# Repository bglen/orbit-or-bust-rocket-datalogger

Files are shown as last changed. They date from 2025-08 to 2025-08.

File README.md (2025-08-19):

# Rocket Datalogger

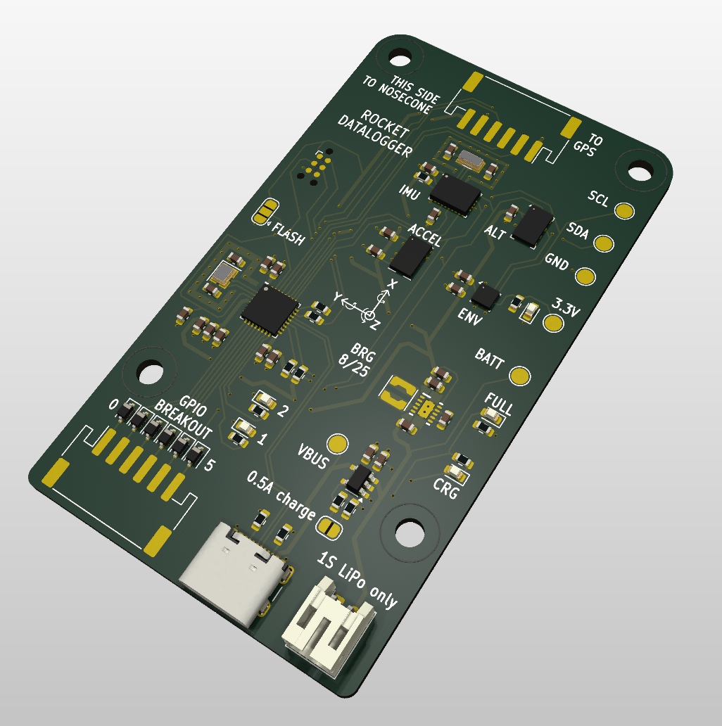
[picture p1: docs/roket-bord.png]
Roket bord


This is an STM32-based model rocket datalogger. It logs from the following sensors:

- DAN-F10-00B ublox dual band GNSS module
- ADXL375 high G accelerometer
- BNO055 9-DOF inertial measurement unit
- MS5607-02BA high resolution altimeter sensor
- BME280 humidity, pressure and temperature sensor

The board is powered from a single 1S LiPo battery with a standard JST-PH connector. A USB-C connector is provided for downloading the flight data. a 6-pin JST-PH connector is provided to extend the device's functionality with 6 3.3V-level GPIO pins.

The GNSS module is on a seperate PCB connected with a JST-PH connector, to give the integrated antenna the appropriate orientation (facing the sky).

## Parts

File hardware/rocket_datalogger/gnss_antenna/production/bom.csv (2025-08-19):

Designator | Footprint | Quantity | Value | LCSC Part #
J1 | JST_PH_S6B-PH-SM4-TB_1x06-1MP_P2.00mm_Horizontal | 1 | JST-PH-S6B-SM4_TB
U1 | DAN-F10-00B | 1 | ~

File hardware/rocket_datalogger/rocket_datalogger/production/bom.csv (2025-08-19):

Designator | Footprint | Quantity | Value | LCSC Part #
C1, C12, C17, C18, C19, C21, C22, C23, C4, C5, C6 | 0603 | 11 | 0.1uF
C10 | 0603 | 1 | 1uF
C11 | 0603 | 1 | 10 uF
C13, C14 | 0603 | 2 | 10uF
C15, C16 | 0603 | 2 | 10uF 6.3V
C2, C3 | 0603 | 2 | 4.7uF
C20 | 0603 | 1 | 1uF Tantalum
C24, C25 | 0603 | 2 | 22 pF
C7, C9 | 0603 | 2 | 12pF
C8 | 0603 | 1 | 10nF
D1, D2, D3, D4, D5, D6 | D_SOD-323 | 6 | PESD3V3L1BA
D10 | 0603 | 1 | Red LED
D11 | 0603 | 1 | Green LED
D7, D8, D9 | 0603 | 3 | LED
J2, J6 | JST_PH_S6B-PH-SM4-TB_1x06-1MP_P2.00mm_Horizontal | 2 | JST-PH-S6B-SM4_TB
J3 | Tag-Connect_TC2030-IDC-NL_2x03_P1.27mm_Vertical | 1 | TC2030
J4 | JST_PH_S2B-PH-K_1x02_P2.00mm_Horizontal | 1 | JST-PH 1x2
J5 | USB_C_Receptacle_GCT_USB4105-xx-A_16P_TopMnt_Horizontal | 1 | USB_C_Receptacle_USB2.0_16P
JP1 | SolderJumper-3_P1.3mm_Open_RoundedPad1.0x1.5mm | 1 | Jumper_3_Open
JP2 | SolderJumper-2_P1.3mm_Open_RoundedPad1.0x1.5mm | 1 | Jumper_2_Open
L1 | L_Coilcraft_LPS3010 | 1 | 1.5uH LPS3015-152MRC
R1, R2 | 0603 | 2 | 5.1k
R10 | 0603 | 1 | 2.2k
R11, R14 | 0603 | 2 | 10k
R12, R13 | 0603 | 2 | 470
R3, R4, R9 | 0603 | 3 | 1k
R5, R6 | 0603 | 2 | 22
R7, R8 | 0603 | 2 | 4.7k
TP1 | TestPoint_Pad_D2.0mm | 1 | TestPoint
TP2 | TestPoint_Pad_D2.0mm | 1 | BATT
TP3 | TestPoint_Pad_D2.0mm | 1 | 3V3
TP4 | TestPoint_Pad_D2.0mm | 1 | GND
TP5 | TestPoint_Pad_D2.0mm | 1 | SCL
TP6 | TestPoint_Pad_D2.0mm | 1 | SDA
U1 | QFN-32-1EP_5x5mm_P0.5mm_EP3.45x3.45mm | 1 | STM32F042K6Ux
U2 | DSK0010A | 1 | ~
U3 | SOT-23-5 | 1 | MCP73831-2-OT
U4 | LGA-8_3x5mm_P1.25mm | 1 | MS5607-02BA
U5 | Bosch_LGA-8_2.5x2.5mm_P0.65mm_ClockwisePinNumbering | 1 | BME280
U7 | LGA-14_3x5mm_P0.8mm_LayoutBorder1x6y | 1 | ~
U8 | LGA-28_5.2x3.8mm_P0.5mm | 1 | BNO055
Y1 | Crystal_SMD_2520-4Pin_2.5x2.0mm | 1 | ECS-160-10-36Q-AES-TR
Y2 | Crystal_SMD_3215-2Pin_3.2x1.5mm | 1 | ECX-.327-CDX-1293

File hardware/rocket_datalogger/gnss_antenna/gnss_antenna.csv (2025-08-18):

Reference | Value | Footprint | Datasheet | Qty | DNP | Exclude from BOM | Exclude from Board
C1,C2 | 4.7uF | Capacitor_SMD:C_0603_1608Metric | ~ | 2
C3,C4,C5,C6,C12,C14,C15 | 0.1uF | Capacitor_SMD:C_0603_1608Metric | ~ | 7
C7,C9 | 12pF | Capacitor_SMD:C_0603_1608Metric | ~ | 2
C8 | 10nF | Capacitor_SMD:C_0603_1608Metric | ~ | 1
C10,C11 | 1uF | Capacitor_SMD:C_0603_1608Metric | ~ | 2
C13 | 22uF | Capacitor_SMD:C_0805_2012Metric | ~ | 1
C16,C17 | 10uF | Capacitor_SMD:C_0603_1608Metric | ~ | 2
D1,D2,D3,D22 | LED | LED_SMD:LED_0603_1608Metric | ~ | 4
D4 | NUP2105L | Package_TO_SOT_SMD:SOT-23 | http://www.onsemi.com/pub_link/Collateral/NUP2105L-D.PDF | 1
D5,D6,D7,D8,D13,D14,D15,D16 | PESD3V3L1BA | Diode_SMD:D_SOD-323 | ~ | 8
D9,D10,D11,D12,D17,D18,D19,D20 | BAT54S | Package_TO_SOT_SMD:SOT-23 | https://www.diodes.com/assets/Datasheets/ds11005.pdf | 8
D21 | CDBW140-G | Diode_SMD:D_SOD-123 | http://www.diodes.com/_files/datasheets/ds23022.pdf | 1
H1,H2,H3,H4 | MountingHole | MountingHole:MountingHole_3.2mm_M3 | ~ | 4 |  | Excluded from BOM
J1 | AMP_Superseal_9-6437287-8 | signal_to_can:TE_9-6437287-8_1 |  | 1
J2 | TC2030 | Connector:Tag-Connect_TC2030-IDC-NL_2x03_P1.27mm_Vertical | ~ | 1
JP1 | Jumper_3_Open | Jumper:SolderJumper-3_P1.3mm_Open_RoundedPad1.0x1.5mm | ~ | 1
R1,R2 | 22 | Resistor_SMD:R_0603_1608Metric | ~ | 2
R3,R4,R5,R14 | 1k | Resistor_SMD:R_0603_1608Metric | ~ | 4
R6,R7,R8,R9,R10,R11,R12,R13 | 6.8k | Resistor_SMD:R_0603_1608Metric | ~ | 8
RV1,RV2,RV3,RV4,RV5,RV6,RV7,RV8 | 3314G-1-503E | Potentiometer_SMD:Potentiometer_Bourns_3314G_Vertical | ~ | 8
TP1 | POWER_INPUT | TestPoint:TestPoint_Pad_D1.0mm | ~ | 1
TP2 | GND | TestPoint:TestPoint_Pad_D1.0mm | ~ | 1
TP3 | 3.3V | TestPoint:TestPoint_Pad_D1.0mm | ~ | 1
TP4 | CAN_TX | TestPoint:TestPoint_Pad_D1.0mm | ~ | 1
TP5 | CAN_RX | TestPoint:TestPoint_Pad_D1.0mm | ~ | 1
TP6 | TestPoint | TestPoint:TestPoint_Pad_D1.0mm | ~ | 1
U1 | STM32F042K6Ux | Package_DFN_QFN:QFN-32-1EP_5x5mm_P0.5mm_EP3.45x3.45mm | http://www.st.com/st-web-ui/static/active/en/resource/technical/document/datasheet/DM00105814.pdf | 1
U2 | TLE42744DV33ATMA1 | Package_TO_SOT_SMD:TO-252-3_TabPin2 |  | 1
U3 | TCAN3403DRQ1 | Package_SO:SOIC-8_3.9x4.9mm_P1.27mm |  | 1
U4 | R-78E5.0-0.5 | Converter_DCDC:Converter_DCDC_RECOM_R-78E-0.5_THT | https://www.recom-power.com/pdf/Innoline/R-78Exx-0.5.pdf | 1
Y1 | ECS-160-10-36Q-AES-TR | Crystal:Crystal_SMD_2520-4Pin_2.5x2.0mm | ~ | 1

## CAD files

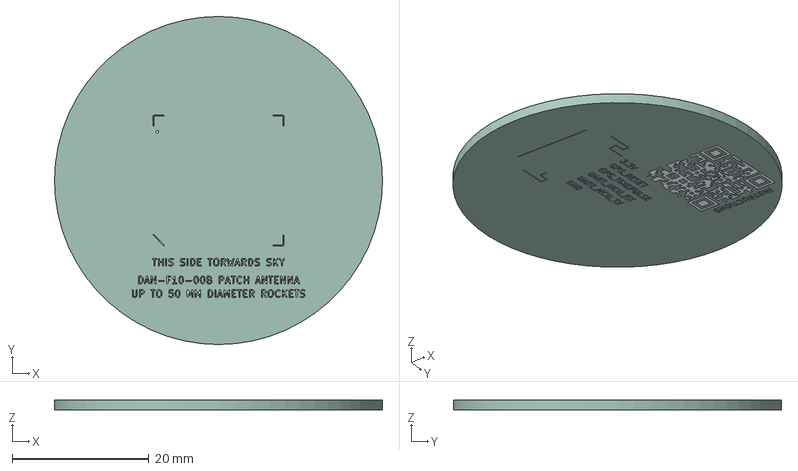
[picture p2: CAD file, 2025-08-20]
hardware/cad/gnss_antenna.step
48.0 x 48.0 x 1.66 mm
gnss_antenna_silkscreen
gnss_antenna_PCB

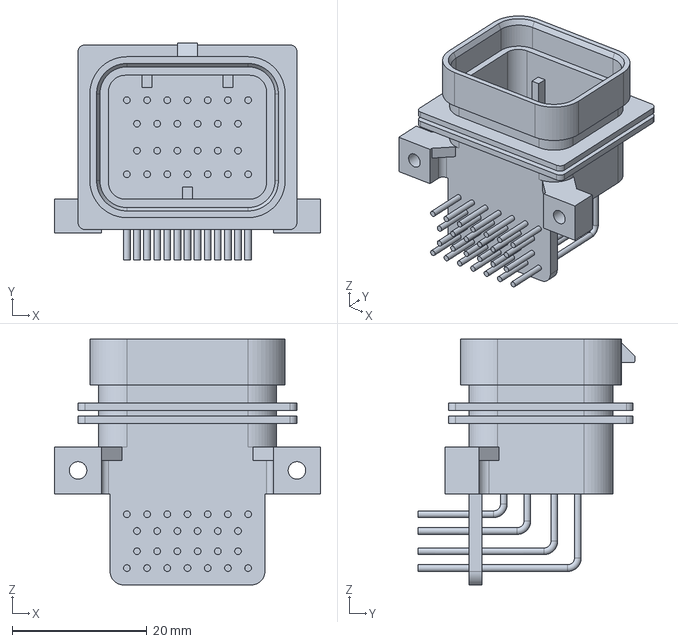
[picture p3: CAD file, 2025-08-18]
hardware/rocket_datalogger/gnss_antenna/3d_models/amp_superseal_9-6437287-8.step
39.5 x 32.1 x 36.5 mm

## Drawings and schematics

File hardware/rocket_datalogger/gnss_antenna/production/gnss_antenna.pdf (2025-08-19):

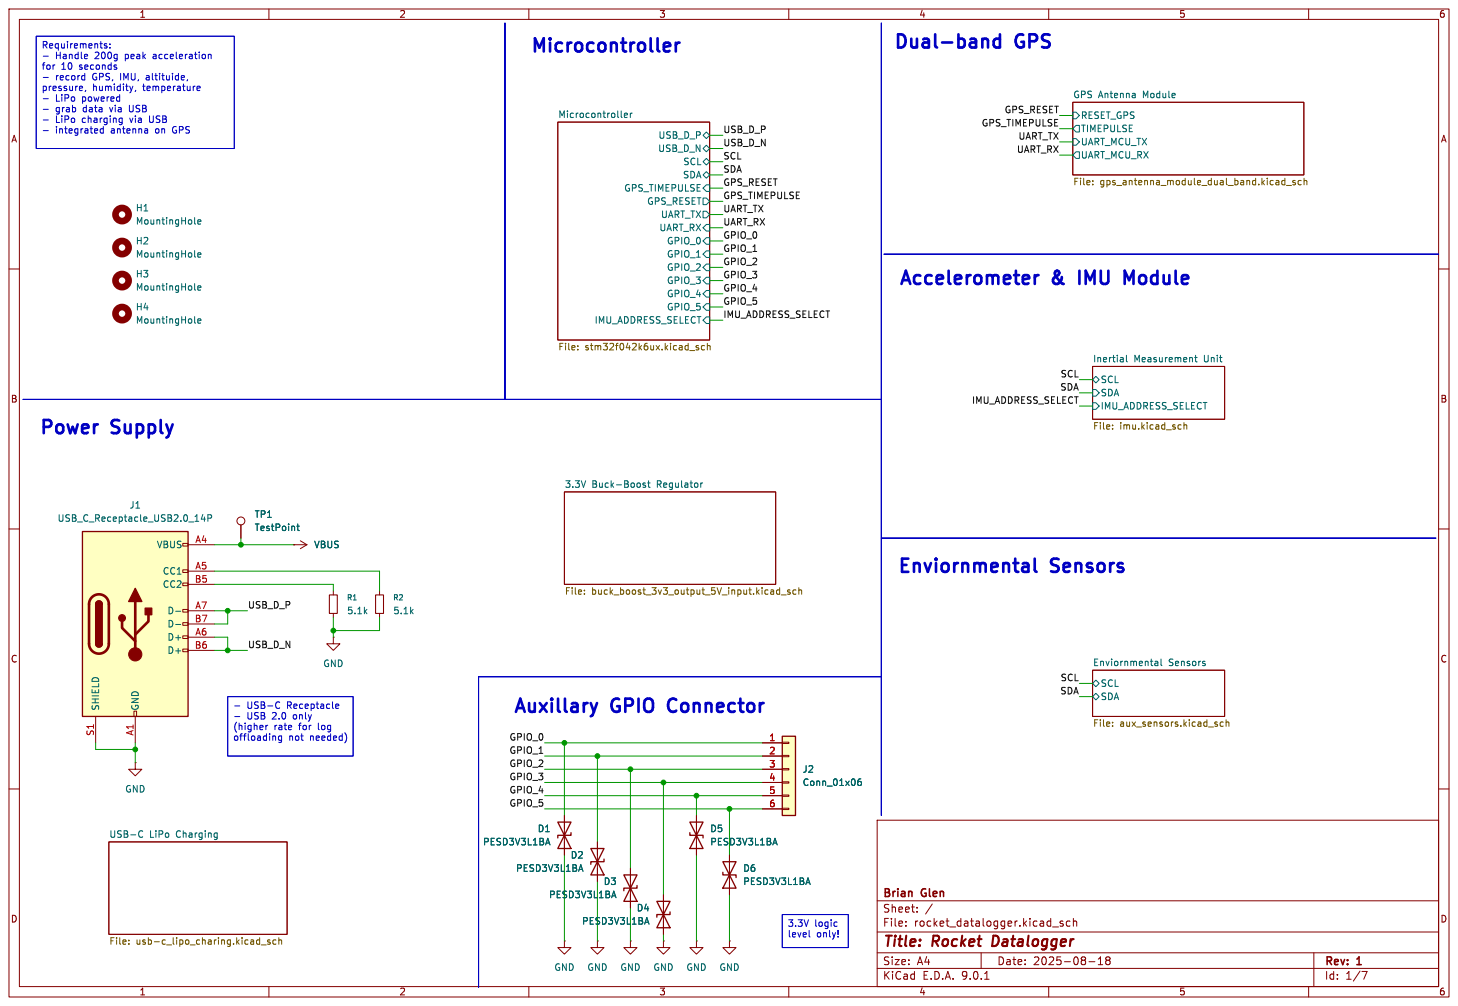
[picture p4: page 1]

Requirements: - Handle 200g peak acceleration

- LiPo powered
- grab data via USB

- USB-C Receptacle
- USB 2.0 only
(higher rate for log

Id: 1/7 Title: Rocket Datalogger File: rocket_datalogger.kicad_sch Sheet: / Brian Glen

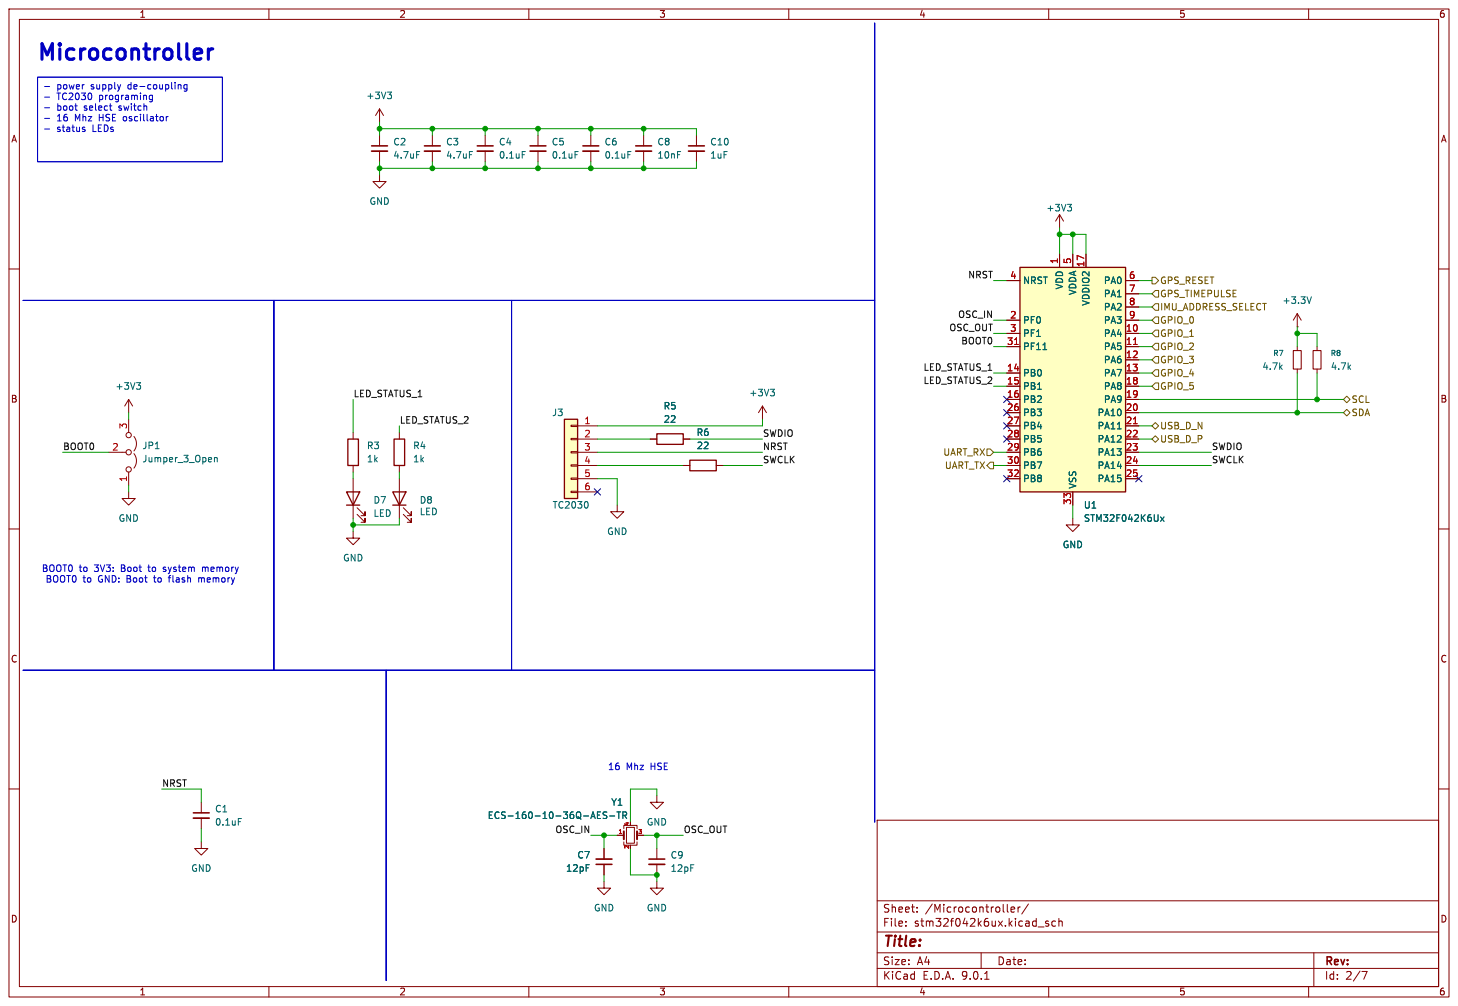
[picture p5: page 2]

- power supply de-coupling
- TC2030 programing
- boot select switch
- 16 Mhz HSE oscillator

5 VSS 33 VDDIO2 17 PA0 6 PA1 7 PA2 8 PA3 9 PA4 10 PA5 11 PA6 12 PA7 13 PA8 18 PA9 19 PA10 20 PA11 21 PA12 22 PA13 23 PA14 24 PA15 25 Y1 ECS-160-10-36Q-AES-TR

3 Y1 ECS-160-10-36Q-AES-TR GND

Id: 2/7 Title: File: stm32f042k6ux.kicad_sch Sheet: /Microcontroller/

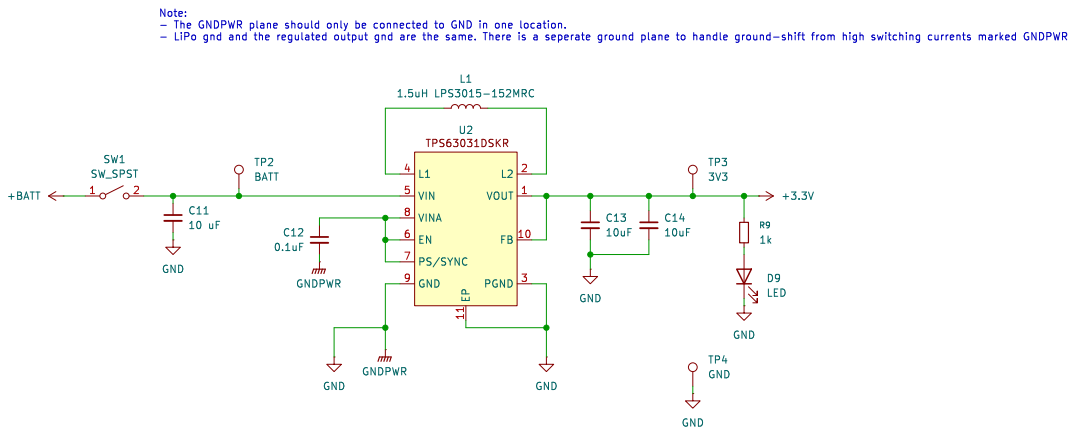
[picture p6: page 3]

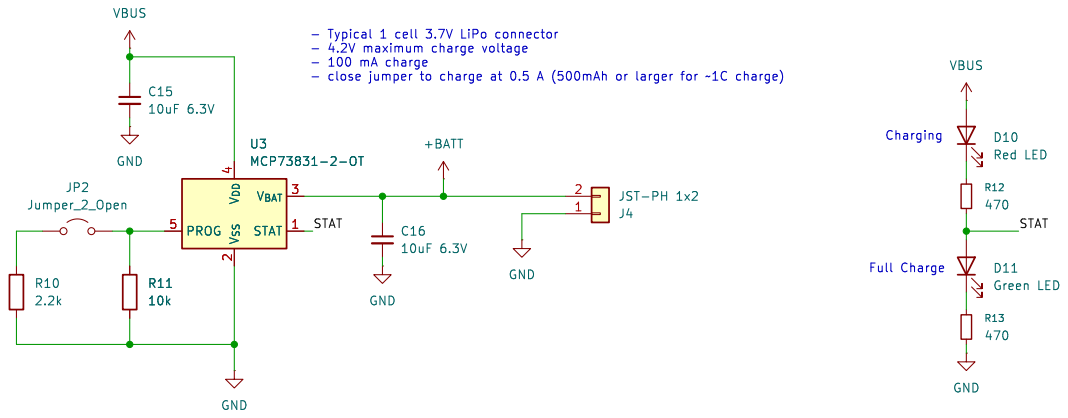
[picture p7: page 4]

- Typical 1 cell 3.7V LiPo connector
- 100 mA charge

- close jumper to charge at 0.5 A (500mAh or larger for ~1C charge) R11

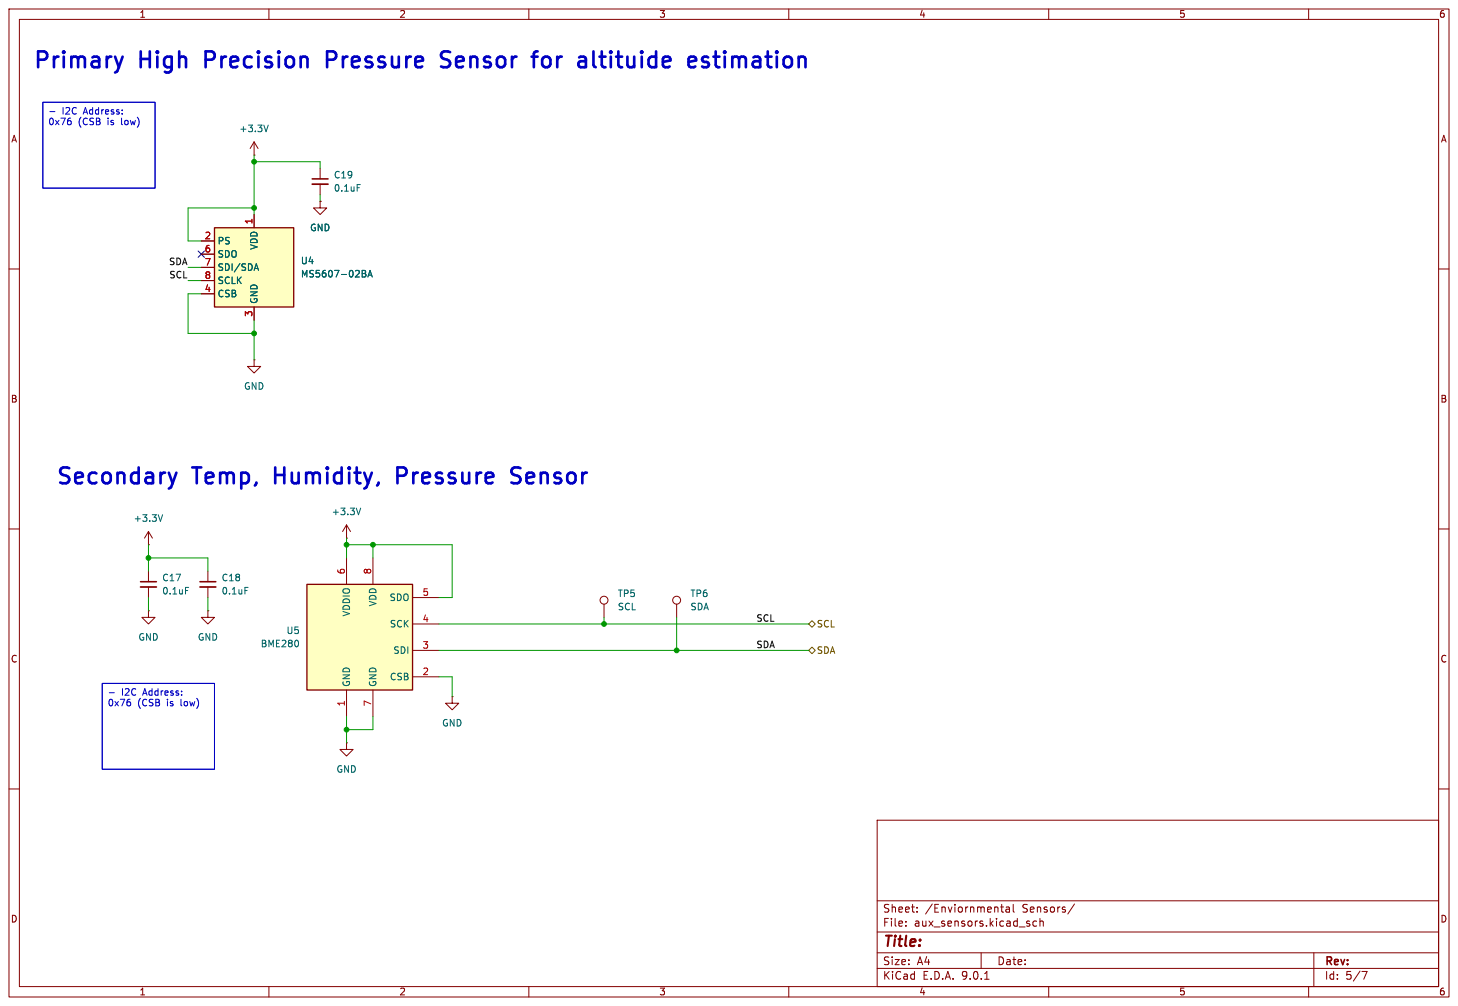
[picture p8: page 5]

- I2C Address: 0x76 (CSB is low)

7 SDO 5 SCK 4 SDI 3 CSB 2 U5 BME280 C18
0.1uF GND

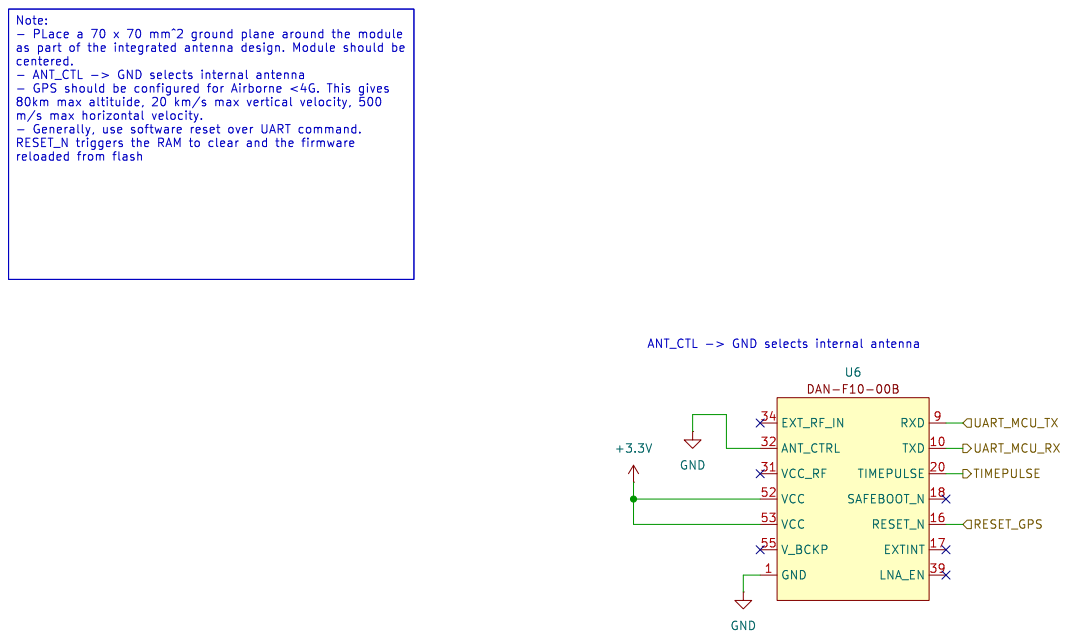
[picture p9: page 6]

TIMEPULSE UART_MCU_TX UART_MCU_RX RESET_GPS Note: - PLace a 70 x 70 mm^2 ground plane around the module

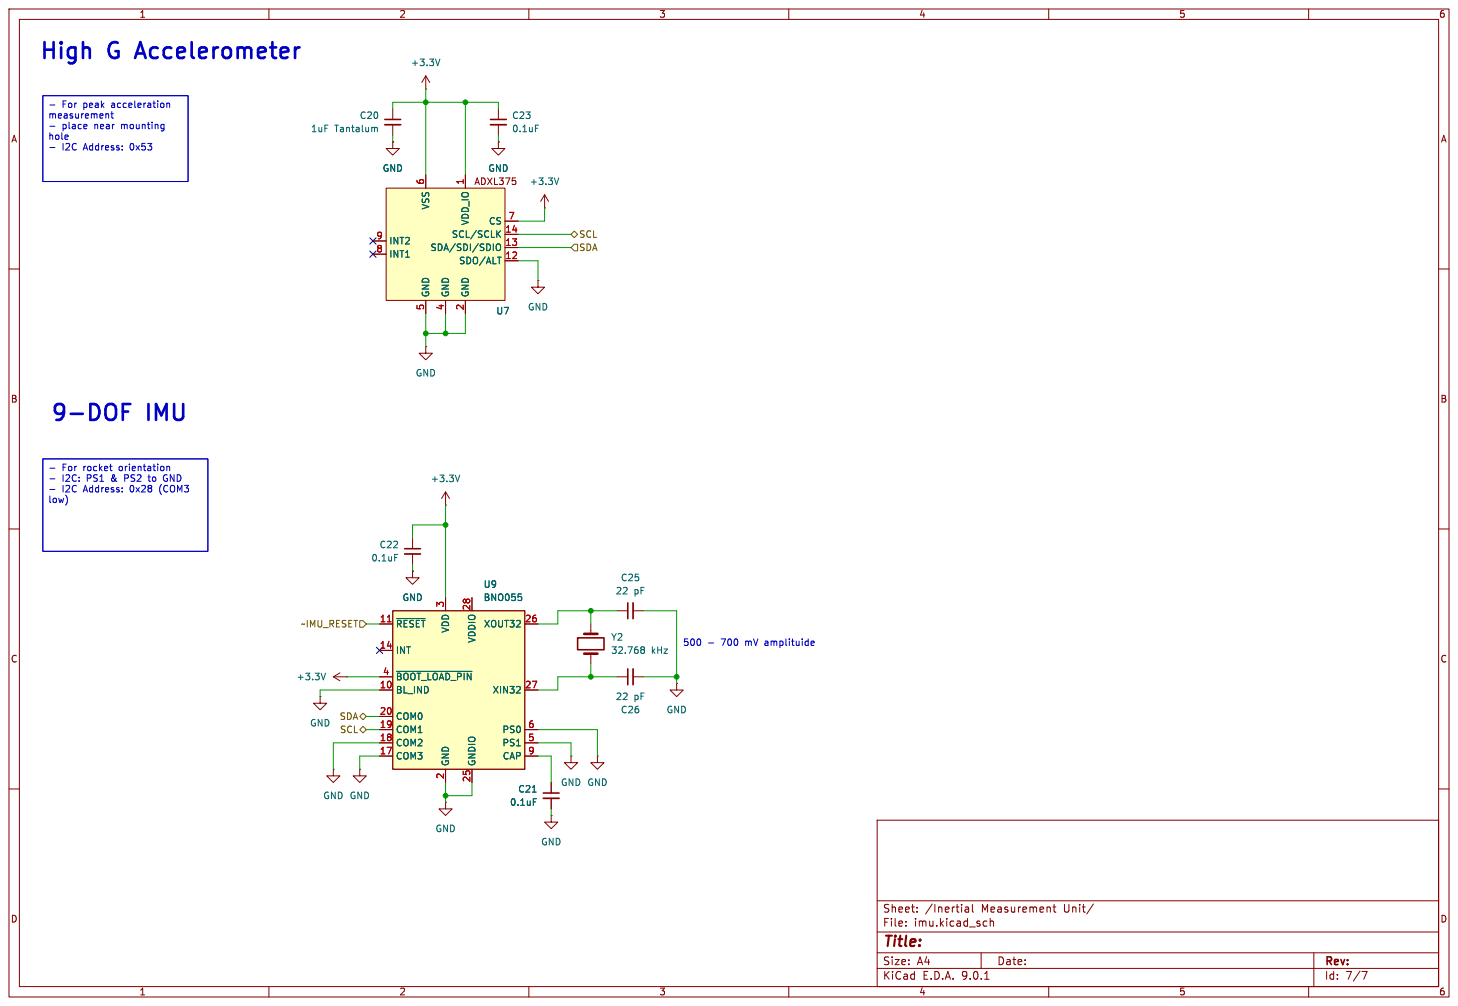
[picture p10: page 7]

- For peak acceleration measurement - place near mounting

2 CS 7 SCL/SCLK 14 SDA/SDI/SDIO 13 SDO/ALT 12 GND GND

2 CS 7 SCL/SCLK 14 SDA/SDI/SDIO 13 SDO/ALT 12 U7 GND

2 VDDIO 28 GNDIO 25 XOUT32 26 XIN32 27 PS0 6 PS1 5 CAP 9 U9 GND BNO055 C22

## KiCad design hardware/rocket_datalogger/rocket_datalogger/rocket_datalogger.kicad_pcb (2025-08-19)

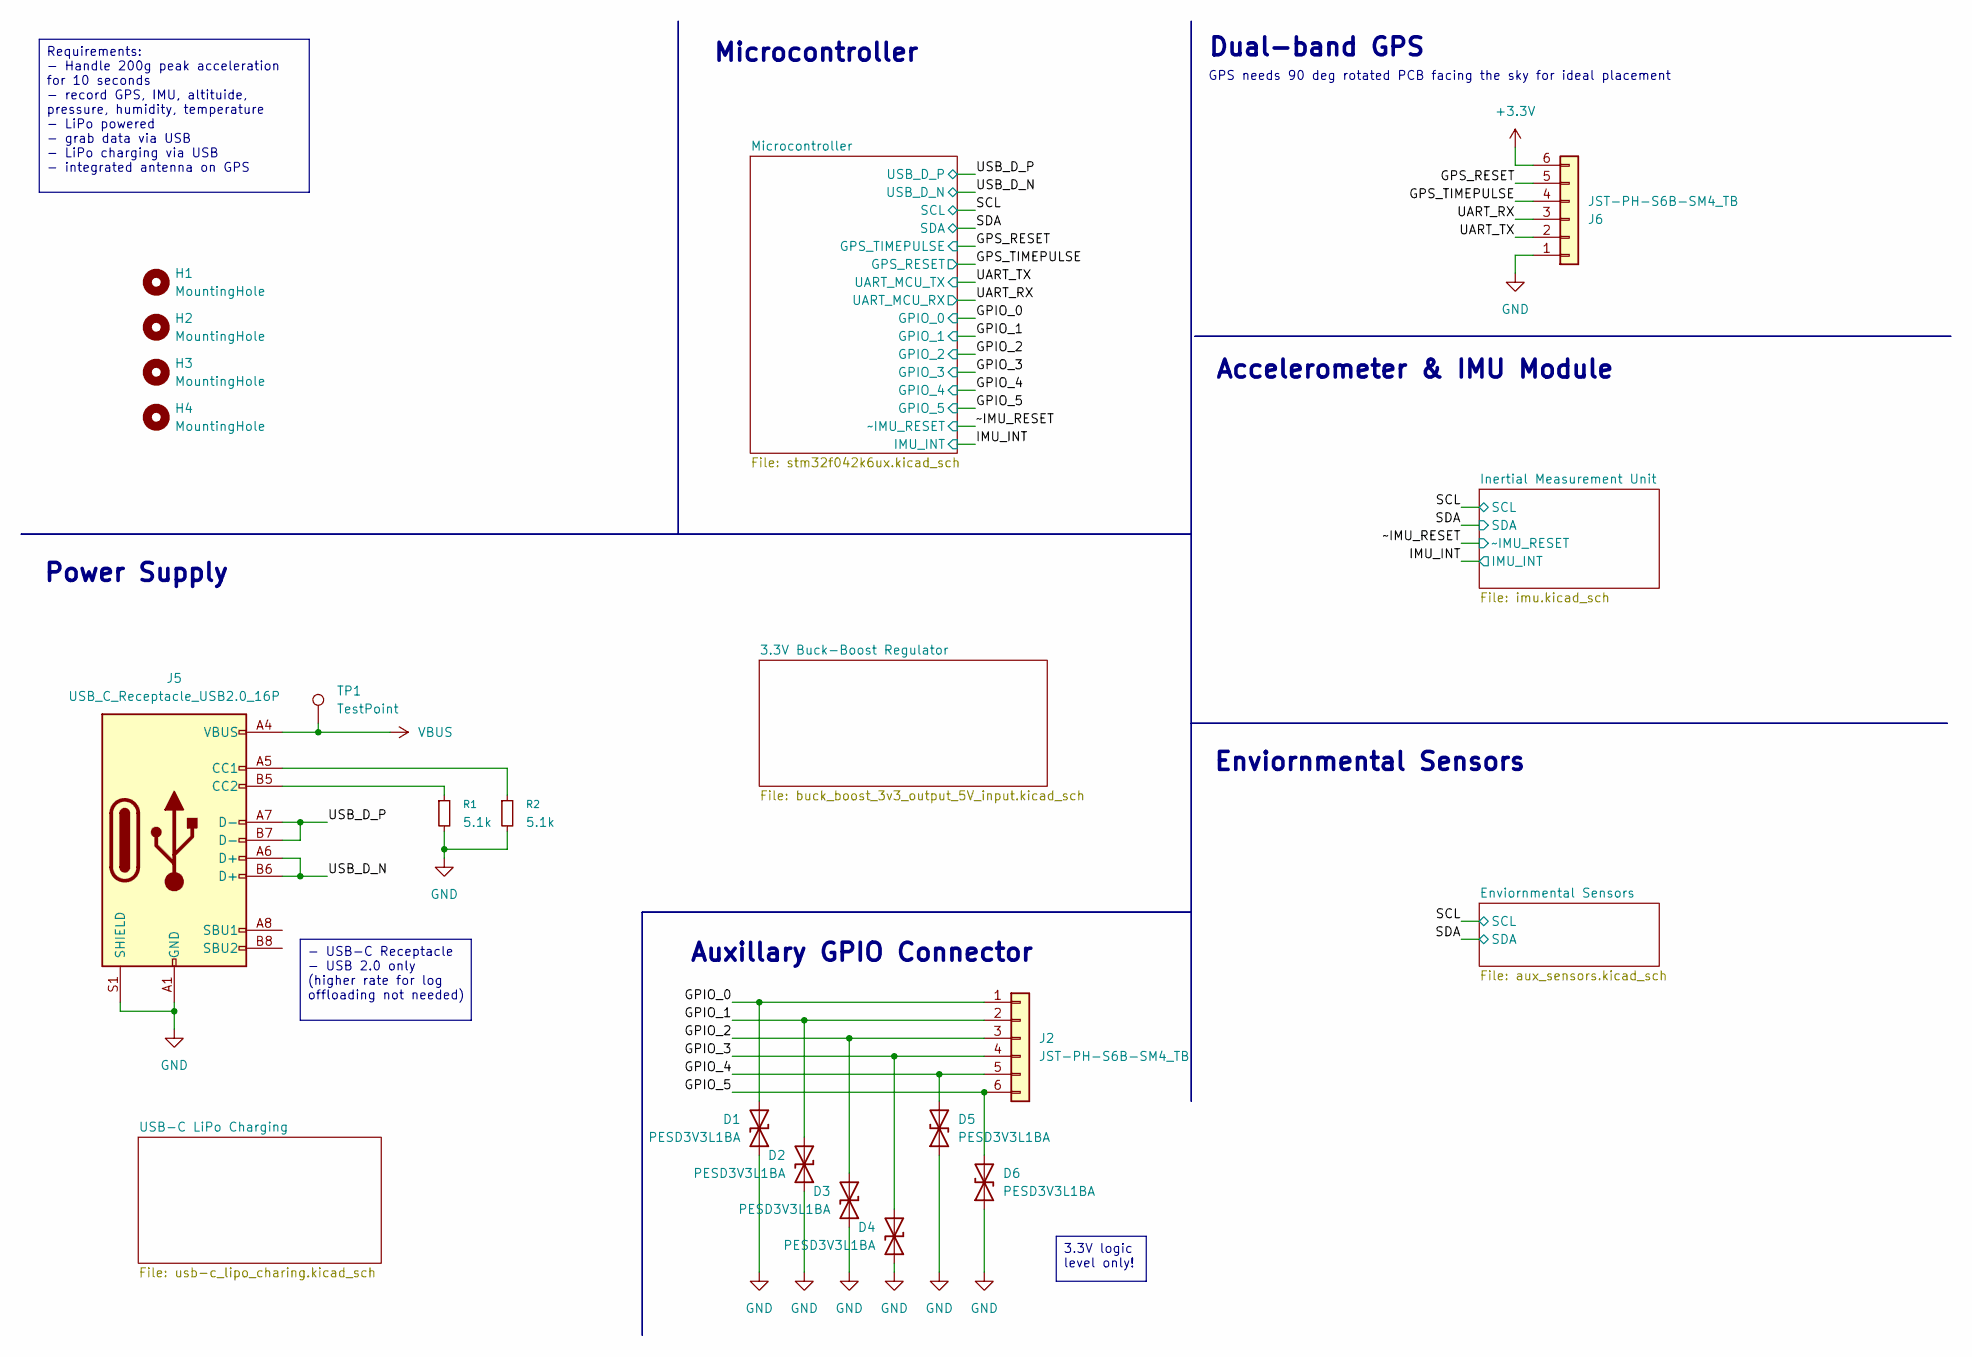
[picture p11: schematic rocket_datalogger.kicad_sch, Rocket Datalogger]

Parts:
D1, D2, D3, D4, D5, D6: PESD3V3L1BA; D_SOD-323
H1, H2, H3, H4: MountingHole; MountingHole_3.2mm_M3
J2, J6: JST-PH-S6B-SM4_TB; JST_PH_S6B-PH-SM4-TB_1x06-1MP_P2.00mm_Horizontal
J5: USB_C_Receptacle_USB2.0_16P; USB_C_Receptacle_GCT_USB4105-xx-A_16P_TopMnt_Horizontal
R1, R2: 5.1k; R_0603_1608Metric
TP1: TestPoint; TestPoint_Pad_D2.0mm

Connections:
+3.3V: J6.6; also elsewhere on the board
/GPIO_0: D1.2 (A2), J2.1; also elsewhere on the board
/GPIO_1: D2.2 (A2), J2.2; also elsewhere on the board
/GPIO_2: D3.2 (A2), J2.3; also elsewhere on the board
/GPIO_3: D4.2 (A2), J2.4; also elsewhere on the board
/GPIO_4: D5.2 (A2), J2.5; also elsewhere on the board
/GPIO_5: D6.2 (A2), J2.6; also elsewhere on the board
/GPS_RESET: J6.5; also elsewhere on the board
/GPS_TIMEPULSE: J6.4; also elsewhere on the board
/UART_RX: J6.3; also elsewhere on the board
/UART_TX: J6.2; also elsewhere on the board
/USB_D_N: J5.A6 (D+), J5.B6 (D+); also elsewhere on the board
/USB_D_P: J5.A7 (D-), J5.B7 (D-); also elsewhere on the board
GND: D1.1 (A1), D2.1 (A1), D3.1 (A1), D4.1 (A1), D5.1 (A1), D6.1 (A1), J5.A1 (GND), J5.A12 (GND), J5.B1 (GND), J5.B12 (GND), J5.S1 (SHIELD), J6.1, R1.2, R2.2; also elsewhere on the board
unnamed: J5.A5 (CC1), R2.1
unnamed: J5.B5 (CC2), R1.1
VBUS: J5.A4 (VBUS), J5.A9 (VBUS), J5.B4 (VBUS), J5.B9 (VBUS), TP1.1; also elsewhere on the board

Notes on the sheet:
Auxillary GPIO Connector
Dual-band GPS
Power Supply
GPS needs 90 deg rotated PCB facing the sky for ideal placement
Enviornmental Sensors
Microcontroller
Accelerometer & IMU Module
- USB-C Receptacle - USB 2.0 only (higher rate for log offloading not needed)
Requirements: - Handle 200g peak acceleration for 10 seconds - record GPS, IMU, altituide, pressure, humidity, temperature - LiPo powered - grab data via USB - LiPo charging via USB - integrated antenna on GPS
3.3V logic level only!

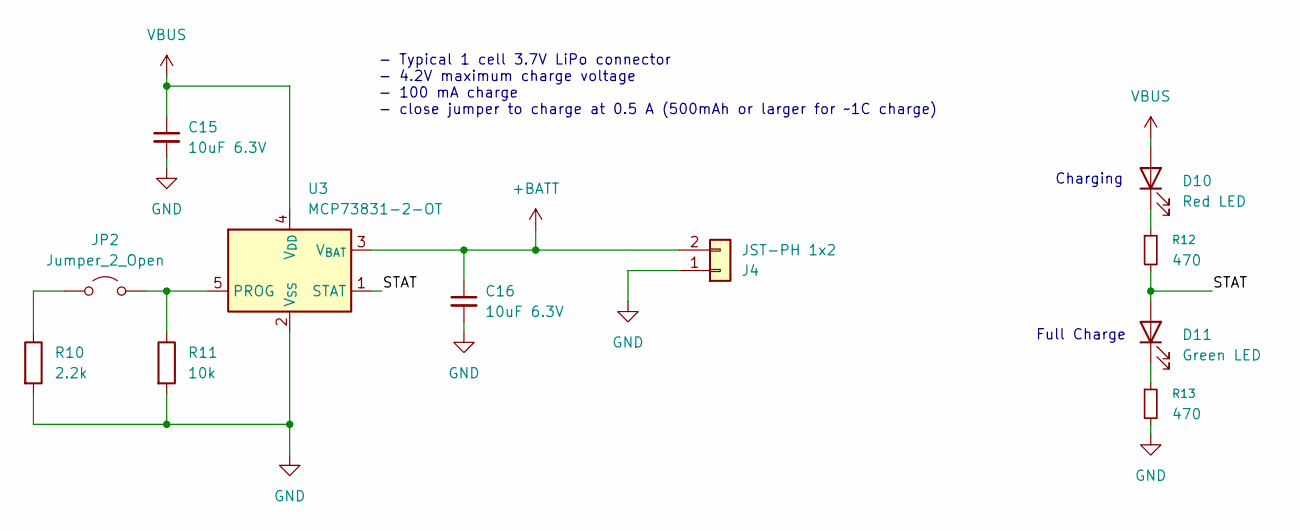
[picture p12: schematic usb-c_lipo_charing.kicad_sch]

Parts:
C15, C16: 10uF 6.3V; C_0603_1608Metric
D10: Red LED; LED_0603_1608Metric
D11: Green LED; LED_0603_1608Metric
J4: JST-PH 1x2; JST_PH_S2B-PH-K_1x02_P2.00mm_Horizontal
JP2: Jumper_2_Open; SolderJumper-2_P1.3mm_Open_RoundedPad1.0x1.5mm
R10: 2.2k; R_0603_1608Metric
R11: 10k; R_0603_1608Metric
R12, R13: 470; R_0603_1608Metric
U3: MCP73831-2-OT; SOT-23-5

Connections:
+BATT: C16.1, J4.2, U3.3 (V_{BAT}); also elsewhere on the board
/USB-C LiPo Charging/STAT: D11.2 (A), R12.2, U3.1 (STAT)
GND: C15.2, C16.2, J4.1, R10.2, R11.2, R13.2, U3.2 (V_{SS}); also elsewhere on the board
unnamed: D10.1 (K), R12.1
unnamed: D11.1 (K), R13.1
unnamed: JP2.1 (A), R10.1
unnamed: JP2.2 (B), R11.1, U3.5 (PROG)
VBUS: C15.1, D10.2 (A), U3.4 (V_{DD}); also elsewhere on the board

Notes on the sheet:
- Typical 1 cell 3.7V LiPo connector - 4.2V maximum charge voltage - 100 mA charge - close jumper to charge at 0.5 A (500mAh or larger for ~1C charge)
Charging
Full Charge

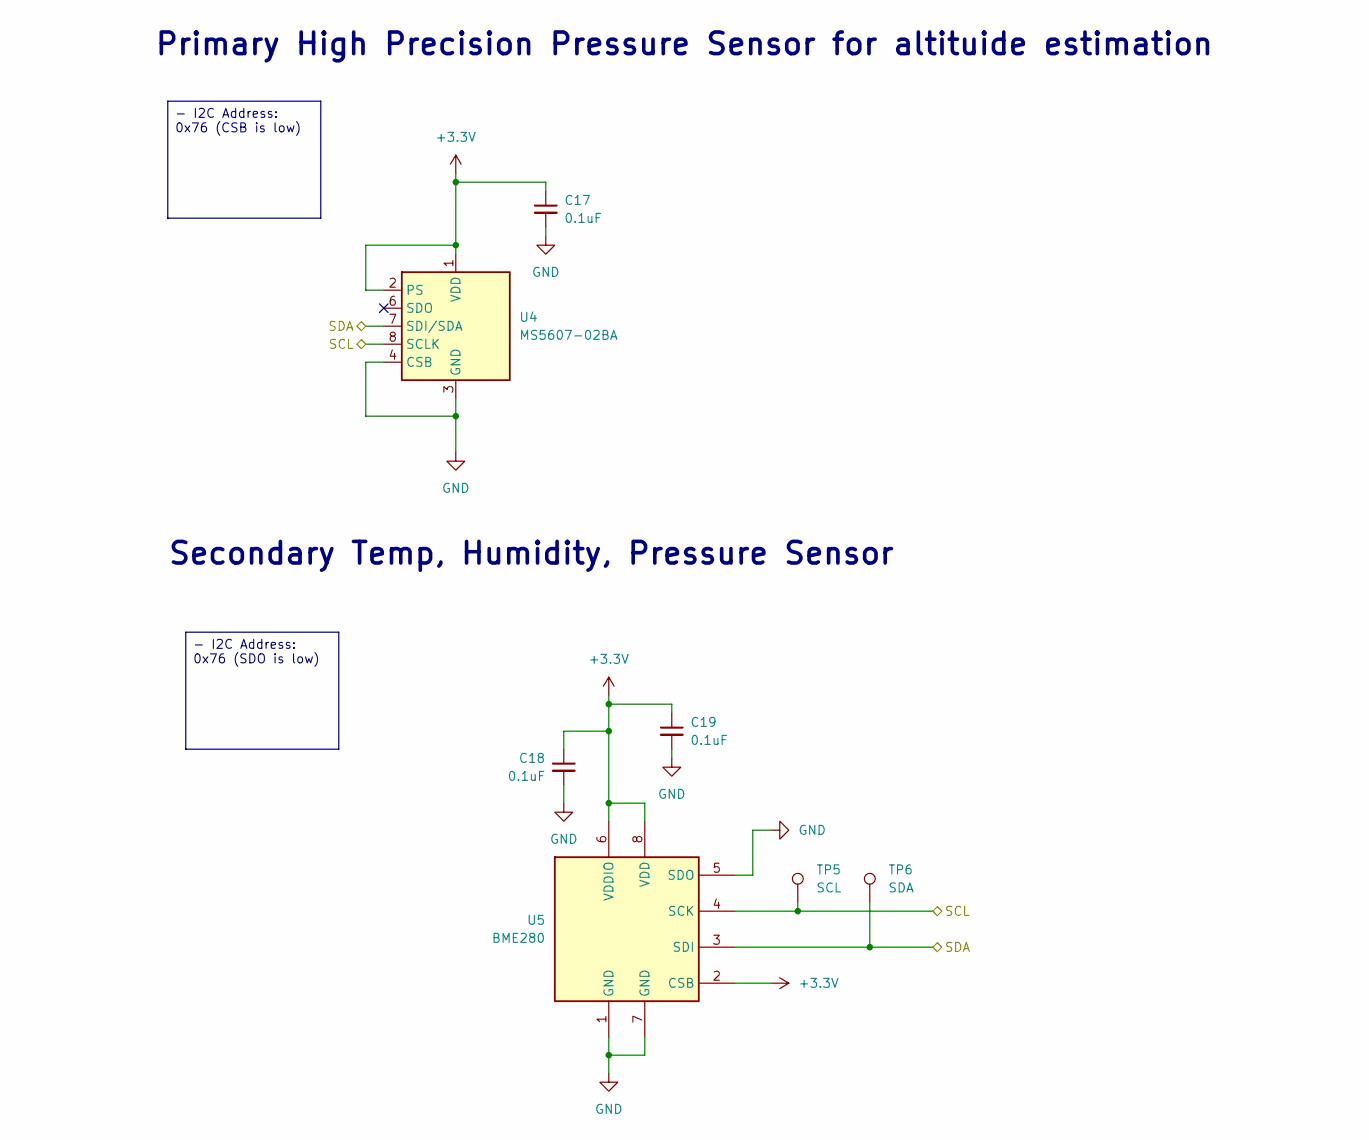
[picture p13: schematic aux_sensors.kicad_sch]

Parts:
C17, C18, C19: 0.1uF; C_0603_1608Metric
TP5: SCL; TestPoint_Pad_D2.0mm
TP6: SDA; TestPoint_Pad_D2.0mm
U4: MS5607-02BA; LGA-8_3x5mm_P1.25mm
U5: BME280; Bosch_LGA-8_2.5x2.5mm_P0.65mm_ClockwisePinNumbering

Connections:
+3.3V: C17.1, C18.1, C19.1, U4.1 (VDD), U4.2 (PS), U5.2 (CSB), U5.6 (VDDIO), U5.8 (VDD); also elsewhere on the board
/SCL: TP5.1, U4.8 (SCLK), U5.4 (SCK); also elsewhere on the board
/SDA: TP6.1, U4.7 (SDI/SDA), U5.3 (SDI); also elsewhere on the board
GND: C17.2, C18.2, C19.2, U4.3 (GND), U4.4 (CSB), U4.5 (CSB), U5.1 (GND), U5.5 (SDO), U5.7 (GND); also elsewhere on the board

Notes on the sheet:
Secondary Temp, Humidity, Pressure Sensor
Primary High Precision Pressure Sensor for altituide estimation
- I2C Address: 0x76 (SDO is low)
- I2C Address: 0x76 (CSB is low)

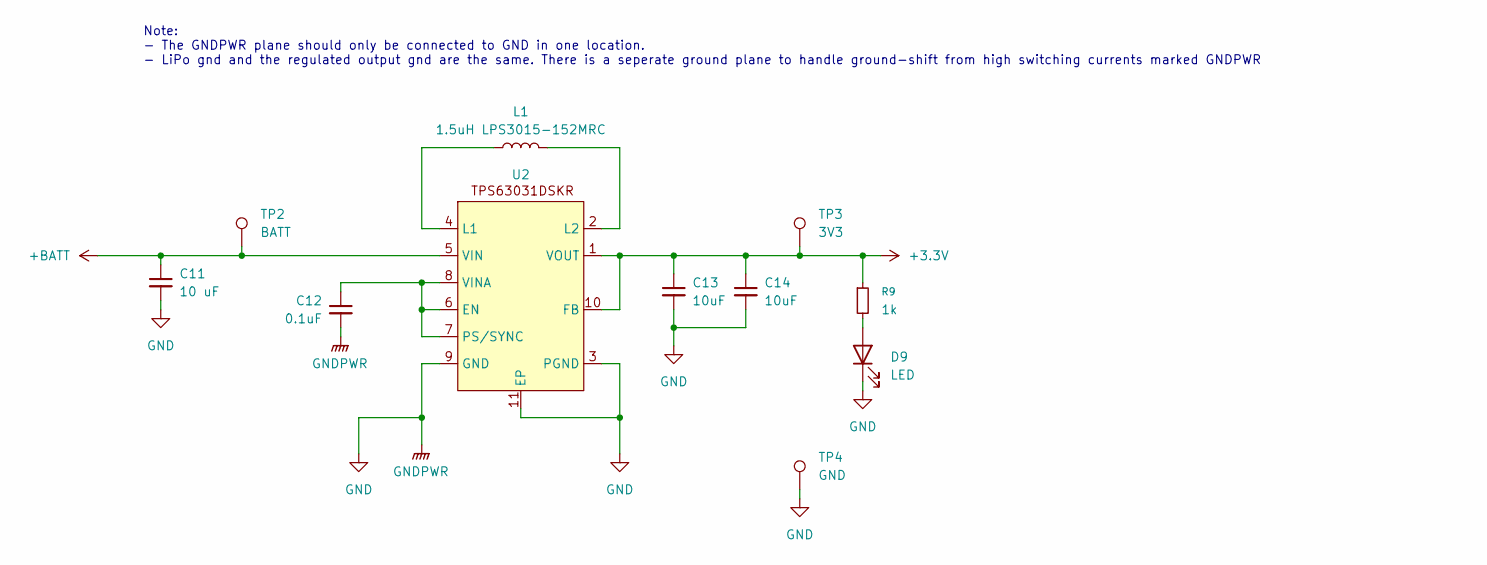
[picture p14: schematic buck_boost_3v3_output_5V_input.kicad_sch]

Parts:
C11: 10 uF; C_0603_1608Metric
C12: 0.1uF; C_0603_1608Metric
C13, C14: 10uF; C_0603_1608Metric
D9: LED; LED_0603_1608Metric
L1: 1.5uH LPS3015-152MRC; L_Coilcraft_LPS3010
R9: 1k; R_0603_1608Metric
TP2: BATT; TestPoint_Pad_D2.0mm
TP3: 3V3; TestPoint_Pad_D2.0mm
TP4: GND; TestPoint_Pad_D2.0mm
U2: DSK0010A

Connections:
+3.3V: C13.1, C14.1, R9.1, TP3.1, U2.1 (VOUT), U2.10 (FB); also elsewhere on the board
+BATT: C11.1, TP2.1, U2.5 (VIN); also elsewhere on the board
GND: C11.2, C12.2, C13.2, C14.2, D9.1 (K), TP4.1, U2.3 (PGND), U2.9 (GND), U2.11 (EP); also elsewhere on the board
unnamed: D9.2 (A), R9.2
unnamed: C12.1, U2.6 (EN), U2.7 (PS/SYNC), U2.8 (VINA)
unnamed: L1.1, U2.4 (L1)
unnamed: L1.2, U2.2 (L2)

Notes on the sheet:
Note: - The GNDPWR plane should only be connected to GND in one location. - LiPo gnd and the regulated output gnd are the same. There is a seperate ground plane to handle ground-shift from high switching currents marked GNDPWR

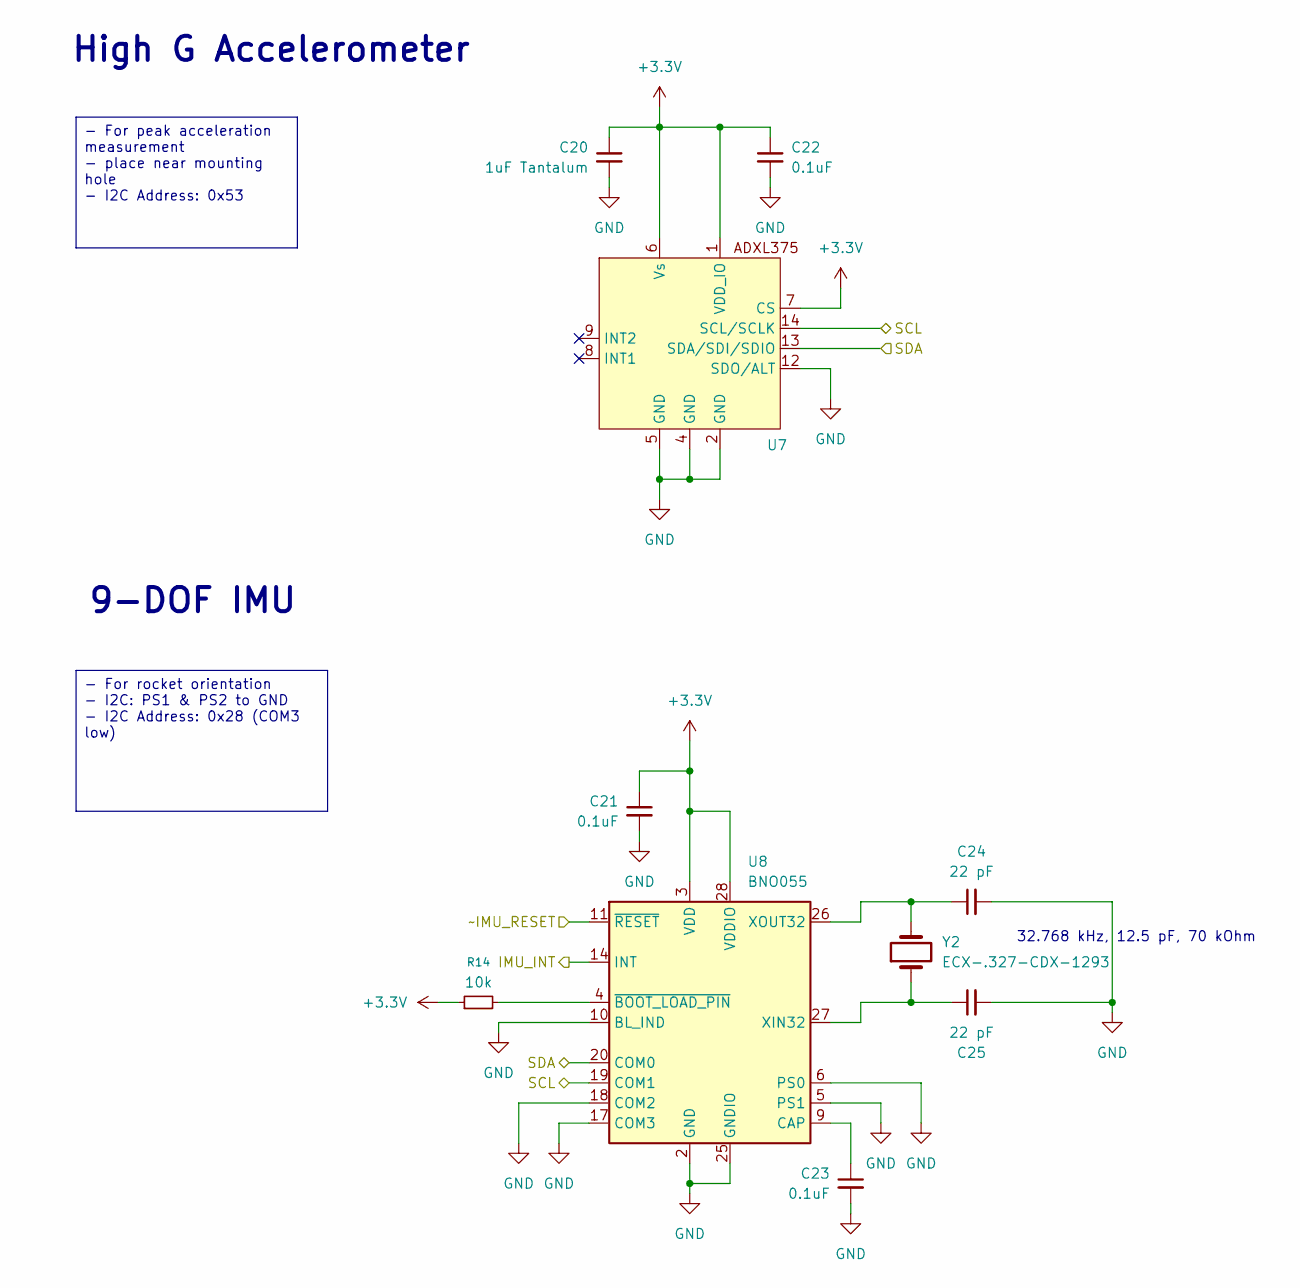
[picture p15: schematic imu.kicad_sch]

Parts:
C20: 1uF Tantalum; C_0603_1608Metric
C21, C22, C23: 0.1uF; C_0603_1608Metric
C24, C25: 22 pF; C_0603_1608Metric
R14: 10k; R_0603_1608Metric
U7: LGA-14_3x5mm_P0.8mm_LayoutBorder1x6y
U8: BNO055; LGA-28_5.2x3.8mm_P0.5mm
Y2: ECX-.327-CDX-1293; Crystal_SMD_3215-2Pin_3.2x1.5mm

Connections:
+3.3V: C20.1, C21.1, C22.1, R14.1, U7.1 (VDD_IO), U7.6 (Vs), U7.7 (CS), U8.3 (VDD), U8.28 (VDDIO); also elsewhere on the board
/IMU_INT: U8.14 (INT); also elsewhere on the board
/SCL: U7.14 (SCL/SCLK), U8.19 (COM1); also elsewhere on the board
/SDA: U7.13 (SDA/SDI/SDIO), U8.20 (COM0); also elsewhere on the board
/~IMU_RESET: U8.11 (~RESET); also elsewhere on the board
GND: C20.2, C21.2, C22.2, C23.2, C24.2, C25.2, U7.2 (GND), U7.4 (GND), U7.5 (GND), U7.12 (SDO/ALT), U8.2 (GND), U8.5 (PS1), U8.6 (PS0), U8.10 (BL_IND), U8.17 (COM3), U8.18 (COM2), U8.25 (GNDIO); also elsewhere on the board
unnamed: C23.1, U8.9 (CAP)
unnamed: C25.1, U8.27 (XIN32), Y2.1
unnamed: C24.1, U8.26 (XOUT32), Y2.2
unnamed: R14.2, U8.4 (~BOOT_LOAD_PIN)

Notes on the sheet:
High G Accelerometer
9-DOF IMU
32.768 kHz, 12.5 pF, 70 kOhm
- For rocket orientation - I2C: PS1 & PS2 to GND - I2C Address: 0x28 (COM3 low)
- For peak acceleration measurement - place near mounting hole - I2C Address: 0x53

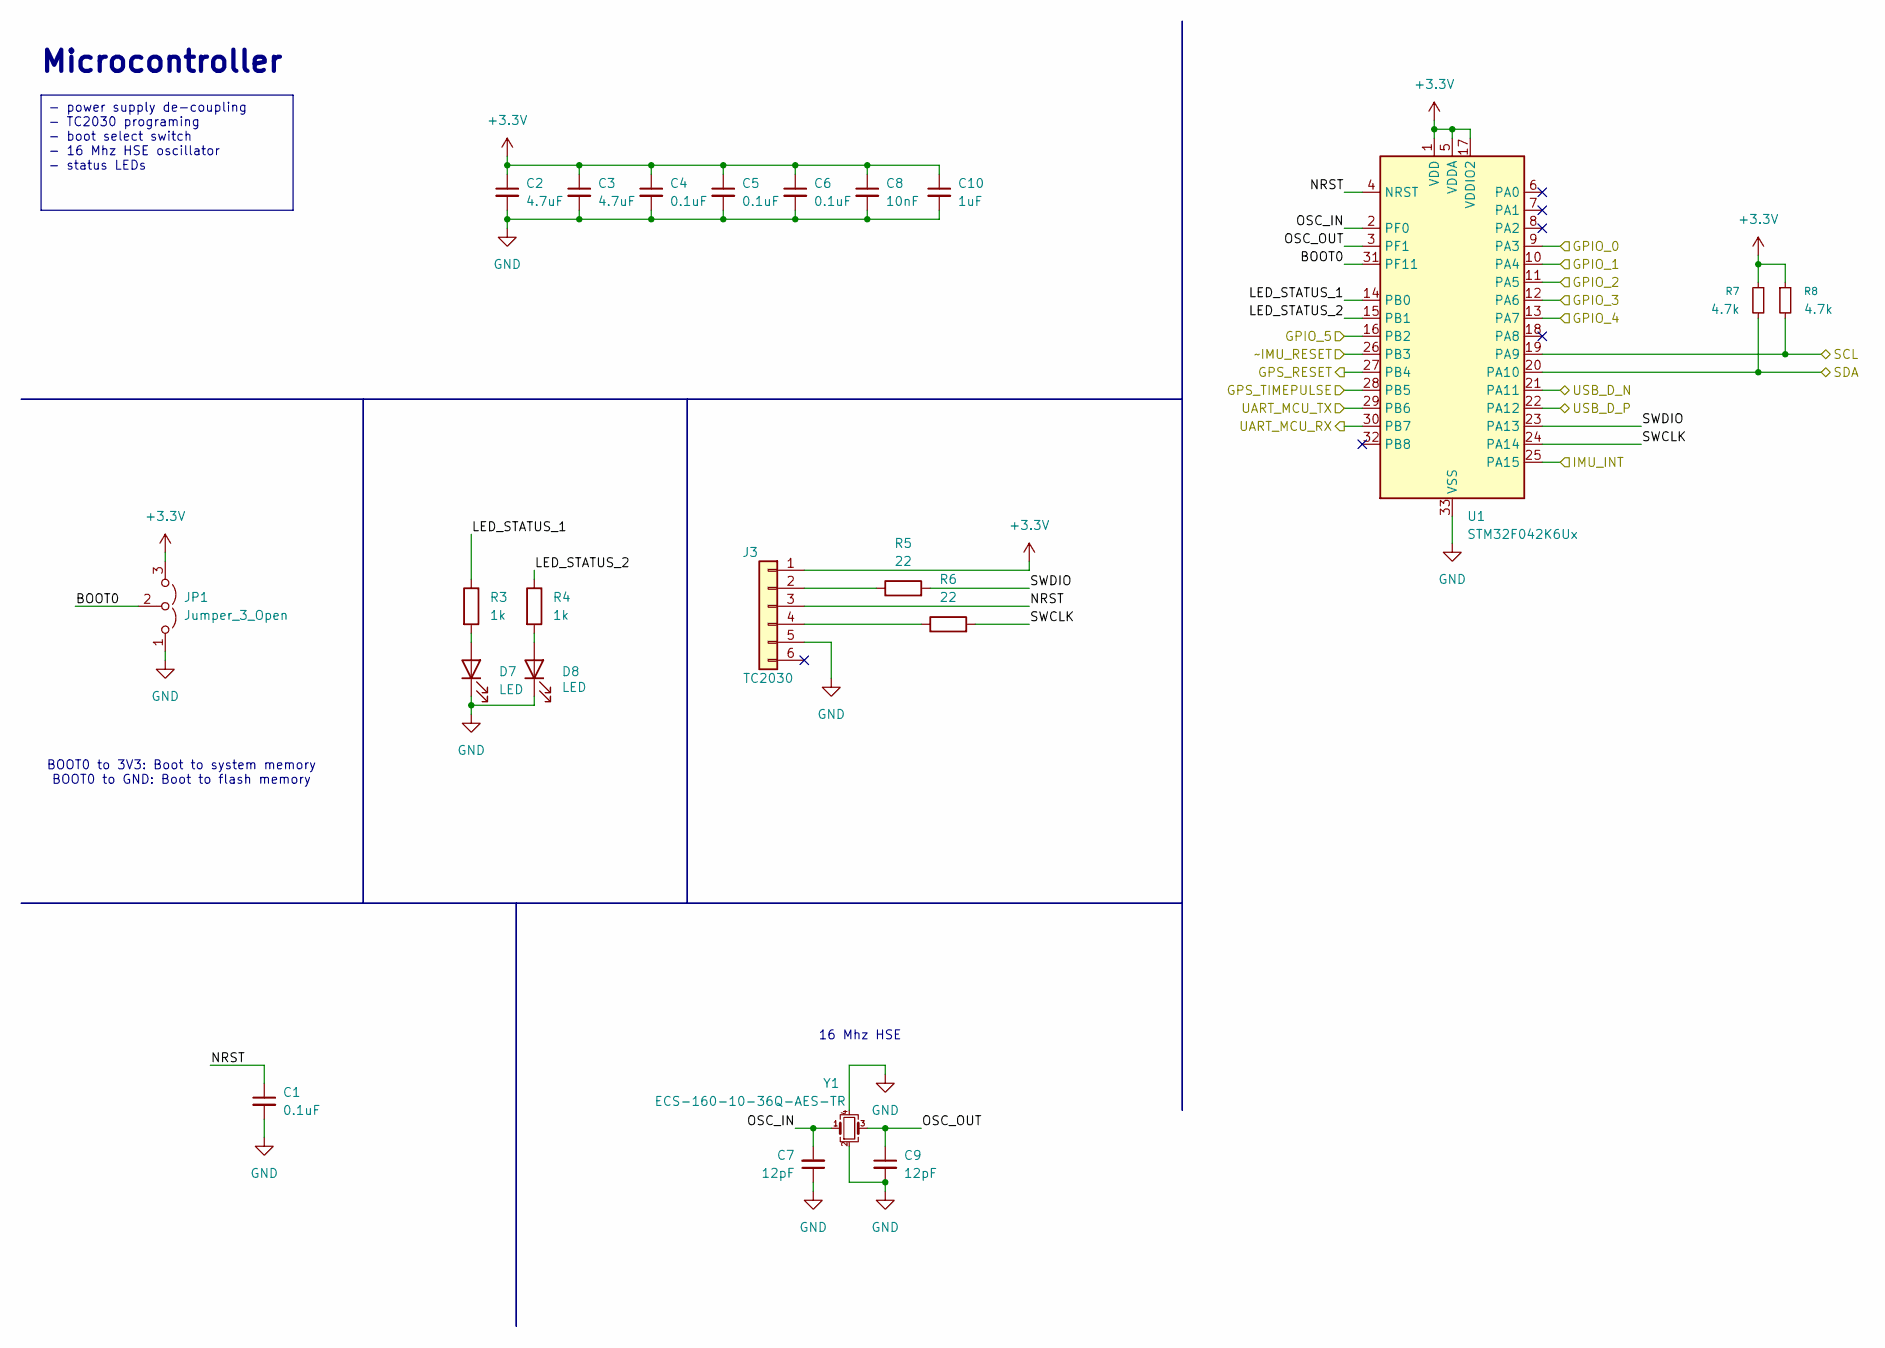
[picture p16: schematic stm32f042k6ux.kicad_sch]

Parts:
C1, C4, C5, C6: 0.1uF; C_0603_1608Metric
C2, C3: 4.7uF; C_0603_1608Metric
C7, C9: 12pF; C_0603_1608Metric
C8: 10nF; C_0603_1608Metric
C10: 1uF; C_0603_1608Metric
D7, D8: LED; LED_0603_1608Metric
J3: TC2030; Tag-Connect_TC2030-IDC-NL_2x03_P1.27mm_Vertical
JP1: Jumper_3_Open; SolderJumper-3_P1.3mm_Open_RoundedPad1.0x1.5mm
R3, R4: 1k; R_0603_1608Metric
R5, R6: 22; R_0603_1608Metric
R7, R8: 4.7k; R_0603_1608Metric
U1: STM32F042K6Ux; QFN-32-1EP_5x5mm_P0.5mm_EP3.45x3.45mm
Y1: ECS-160-10-36Q-AES-TR; Crystal_SMD_2520-4Pin_2.5x2.0mm

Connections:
+3.3V: C2.1, C3.1, C4.1, C5.1, C6.1, C8.1, C10.1, J3.1, JP1.3 (B), R7.1, R8.1, U1.1 (VDD), U1.5 (VDDA), U1.17 (VDDIO2); also elsewhere on the board
/GPIO_0: U1.9 (PA3); also elsewhere on the board
/GPIO_1: U1.10 (PA4); also elsewhere on the board
/GPIO_2: U1.11 (PA5); also elsewhere on the board
/GPIO_3: U1.12 (PA6); also elsewhere on the board
/GPIO_4: U1.13 (PA7); also elsewhere on the board
/GPIO_5: U1.16 (PB2); also elsewhere on the board
/GPS_RESET: U1.28 (PB5); also elsewhere on the board
/GPS_TIMEPULSE: U1.27 (PB4); also elsewhere on the board
/IMU_INT: U1.25 (PA15); also elsewhere on the board
/Microcontroller/BOOT0: JP1.2 (C), U1.31 (PF11)
/Microcontroller/LED_STATUS_1: R3.1, U1.14 (PB0)
/Microcontroller/LED_STATUS_2: R4.1, U1.15 (PB1)
/Microcontroller/NRST: C1.1, J3.3, U1.4 (NRST)
/Microcontroller/OSC_IN: C7.2, U1.2 (PF0), Y1.1
/Microcontroller/OSC_OUT: C9.1, U1.3 (PF1), Y1.3
/Microcontroller/SWCLK: R6.2, U1.24 (PA14)
/Microcontroller/SWDIO: R5.2, U1.23 (PA13)
/SCL: R8.2, U1.19 (PA9); also elsewhere on the board
/SDA: R7.2, U1.20 (PA10); also elsewhere on the board
/UART_RX: U1.30 (PB7); also elsewhere on the board
/UART_TX: U1.29 (PB6); also elsewhere on the board
/USB_D_N: U1.21 (PA11); also elsewhere on the board
/USB_D_P: U1.22 (PA12); also elsewhere on the board
/~IMU_RESET: U1.26 (PB3); also elsewhere on the board
GND: C1.2, C2.2, C3.2, C4.2, C5.2, C6.2, C7.1, C8.2, C9.2, C10.2, D7.1 (K), D8.1 (K), J3.5, JP1.1 (A), U1.33 (VSS), Y1.2, Y1.4; also elsewhere on the board
unnamed: D7.2 (A), R3.2
unnamed: D8.2 (A), R4.2
unnamed: J3.2, R5.1
unnamed: J3.4, R6.1

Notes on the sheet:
BOOT0 to 3V3: Boot to system memory BOOT0 to GND: Boot to flash memory
Microcontroller
16 Mhz HSE
- power supply de-coupling - TC2030 programing - boot select switch - 16 Mhz HSE oscillator - status LEDs

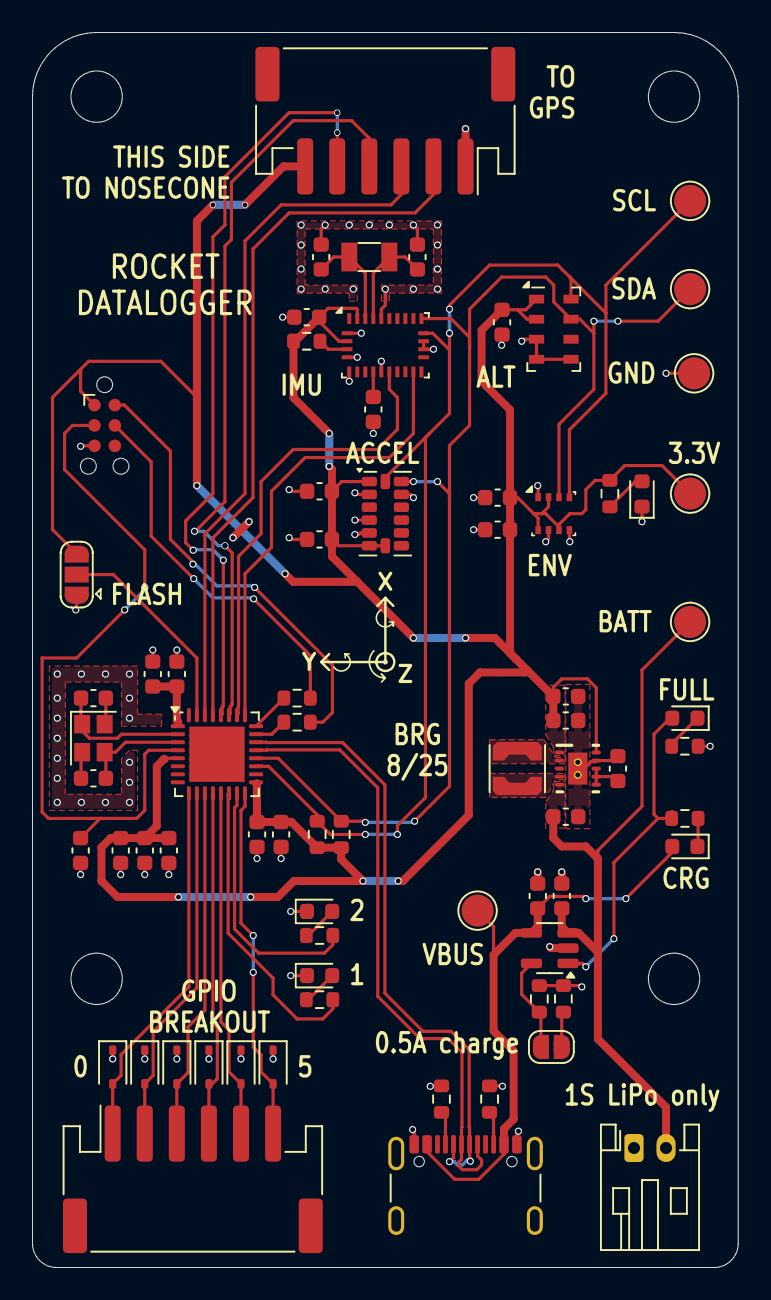
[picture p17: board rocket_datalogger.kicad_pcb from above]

Board: 2 copper layers, 44.0 x 77.0 mm, 77 parts (0 on the bottom side), 47 nets.

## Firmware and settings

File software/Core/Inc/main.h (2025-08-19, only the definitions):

#define GPS_RESET_Pin GPIO_PIN_0
#define GPS_RESET_GPIO_Port GPIOA
#define GPS_TIMEPULSE_Pin GPIO_PIN_1
#define GPS_TIMEPULSE_GPIO_Port GPIOA
#define IMU_ADDRESS_SELECT_Pin GPIO_PIN_2
#define IMU_ADDRESS_SELECT_GPIO_Port GPIOA
#define GPIO_0_Pin GPIO_PIN_3
#define GPIO_0_GPIO_Port GPIOA
#define GPIO_1_Pin GPIO_PIN_4
#define GPIO_1_GPIO_Port GPIOA
#define GPIO_2_Pin GPIO_PIN_5
#define GPIO_2_GPIO_Port GPIOA
#define GPIO_3_Pin GPIO_PIN_6
#define GPIO_3_GPIO_Port GPIOA
#define GPIO_4_Pin GPIO_PIN_7
#define GPIO_4_GPIO_Port GPIOA
#define LED_STATUS_1_Pin GPIO_PIN_0
#define LED_STATUS_1_GPIO_Port GPIOB
#define LED_STATUS_2_Pin GPIO_PIN_1
#define LED_STATUS_2_GPIO_Port GPIOB
#define GPIO_5_Pin GPIO_PIN_2
#define GPIO_5_GPIO_Port GPIOB

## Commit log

2025-08-18 Initial hardware commit
    [amp_superseal_9-6437287-8.step, aux_sensors.kicad_sch, buck_boost_3v3_output_5V_input.kicad_sch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]
2025-08-19 Changed IMU to BNO055
    Previous IMU required 1.85V rail
    [aux_sensors.kicad_sch, buck_boost_3v3_output_5V_input.kicad_sch, gps_antenna_module_dual_band.kicad_sch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]
2025-08-19 fixed minor hardware issues
    [aux_sensors.kicad_sch, buck_boost_3v3_output_5V_input.kicad_sch, gps_antenna_module_dual_band.kicad_sch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]
2025-08-19 Minor revision
    [aux_sensors.kicad_sch, buck_boost_3v3_output_5V_input.kicad_sch, gps_antenna_module_dual_band.kicad_sch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]
2025-08-19 PCB design rev 1
    [bom.csv, buck_boost_3v3_output_5V_input.kicad_sch, designators.csv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]
2025-08-19 GNSS Antenna board
    [amp_superseal_9-6437287-8.step, bom.csv, designators.csv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]
2025-08-19 Updated BOM and schematic notes
    [rocket_datalogger.kicad_sch, stm32f042k6ux.kicad_sch]
2025-08-20 PCB step files
    [gnss_antenna.step]

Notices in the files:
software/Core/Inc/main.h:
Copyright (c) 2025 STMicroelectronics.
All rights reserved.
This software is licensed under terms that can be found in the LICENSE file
